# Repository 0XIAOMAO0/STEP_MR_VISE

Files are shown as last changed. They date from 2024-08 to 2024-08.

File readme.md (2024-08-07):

# 电动小台钳

## 项目介绍

本项目使用CNC板材及一些机械零件制作了一个电动焊接台钳。CNC器件在嘉立创1元CNC打样活动打样，驱动部分使用闭环步进驱动，电机驱动板适用35步进电机。可用于其他项目。计划实现功能

+ 台钳位置闭环

+ 按键设定位置

+ 夹持电流自动调整(待做)

+ 长时间自动休眠(待做)

+ 外面控制输入(待做)

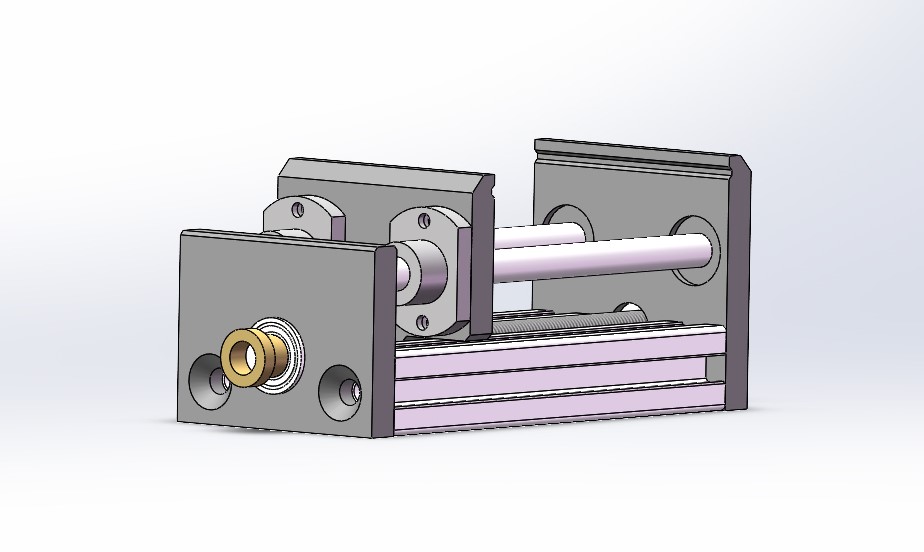
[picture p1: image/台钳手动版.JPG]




视频演示：[bilibili](https://www.bilibili.com/video/BV1ybicebESk/?share_source=copy_web&vd_source=d128331ee99153cf5294c26aba5f51e4) 

软件开源地址：[github](https://github.com/0XIAOMAO0/STEP_MR_VISE)   软件部分参考["矛盾聚合体"](https://gitee.com/STM32G474RET6/cl-stepper-motor)  

硬件开源地址: [oshwhub](http://oshwhub.com/xaiomao/tai-qian-kong-zhi-ban)硬件部分参考["HyperStepper"](https://oshwhub.com/HyperCNC/yi-ti-hua-di-cheng-ben-gao-su-gao-jing-du-quan-bi-huan-bu-jin-dian-ji)

## 材料清单

1.电路板所需元器件BOM已给出

2.结构部分：

|编号| 名称 | 个数 | 链接 |
|-|--- | ---- | --- |
| 1 |CNC铝板 | 3 | 嘉立创CNC打样 |
| 2 |2020铝型材120mm两端攻牙M6 | 2 | [参考连接]([欧标2020工业铝型材2040/2060/2080V槽黑色铝合金型材3D打印框架-淘宝网 (taobao.com)](https://item.taobao.com/item.htm?id=679620555797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..)) |
| 3 |8mm光轴130mm(两端不能有毛刺) | 2 | [参考链接]([45#钢直线导轨轴承20光轴镀铬棒加工高精度圆柱硬轴软轴活塞光杆-淘宝网 (taobao.com)](https://item.taobao.com/item.htm?id=707072898042&ft=t)) |
| 4 |双切边法兰直线轴承8x15x24 | 2 | [参考连接]([双切边椭圆法兰直线轴承中间型加长LMHC10 12 16 20 25 30 40 LUU-淘宝网 (taobao.com)](https://item.taobao.com/item.htm?id=674397062232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)) |
| 5 |T8丝杆143mm螺距2导程8 | 1 | [参考连接]([铭泰3d打印机配件T型T8丝杆步进电机丝杠螺母梯形螺杆不锈钢导程8-淘宝网 (taobao.com)](https://item.taobao.com/item.htm?id=573812002249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..)) |
| 6 |微型法兰轴承F688Z（8*18 *5） | 手动:2 / 电动:1 | [参考连接]([铭泰 3D打印机配件 微型带法兰直线轴承 F623 624 604 625 688ZZ-淘宝网 (taobao.com)](https://item.taobao.com/item.htm?id=574092180169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)) |
| 7 |消隙螺母T8导程8 | 1 | [参考连接]([3D打印机配件T8丝杆切边螺母铜消间隙消回差螺母梯型不锈钢丝杆-淘宝网 (taobao.com)](https://item.taobao.com/item.htm?id=648455763916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..)) |
| 8 |T8丝杆丝杆螺母螺距2导程8 | 1(一般买丝杆赠送) | [参考连接]([铭泰3d打印机配件T型T8丝杆步进电机丝杠螺母梯形螺杆不锈钢导程8-淘宝网 (taobao.com)](https://item.taobao.com/item.htm?id=573812002249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..)) |
| 9 |联轴器5*8 | 手动:0 / 电动:1 | [参考连接]([铭泰3D打印机配件铝合金联轴器 电机车膜船航模联轴器金属模型DIY-淘宝网 (taobao.com)](https://item.taobao.com/item.htm?id=570850575149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..)) |
| 10 |M6x14螺丝 | 4 |  |
| 11 |M3*12 *4(头径)小头螺丝 | 10 |  |
| 12 | 35步进电机 | 手动:0 / 电动:1 ||

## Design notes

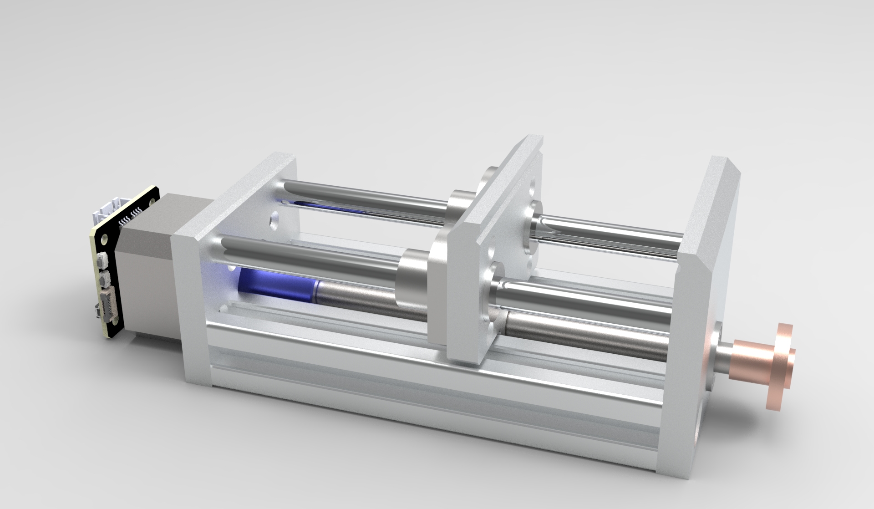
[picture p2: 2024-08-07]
image/渲染图.jpg

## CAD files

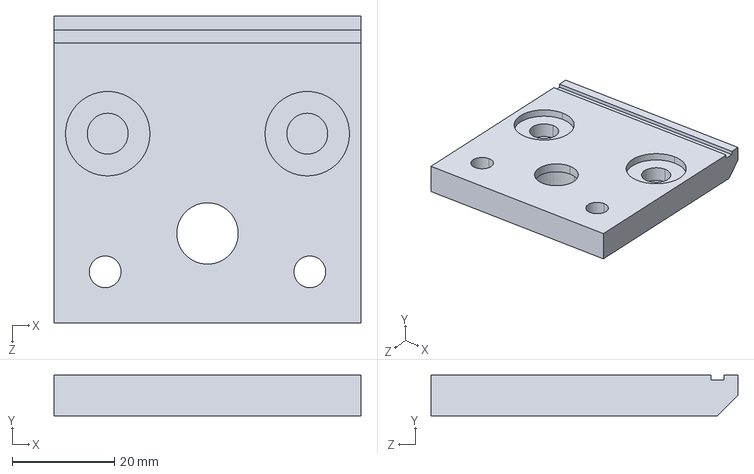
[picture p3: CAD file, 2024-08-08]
model/打样文件/修改版/修改版_固定钳身.STEP
60.0 x 8.00 x 60.0 mm

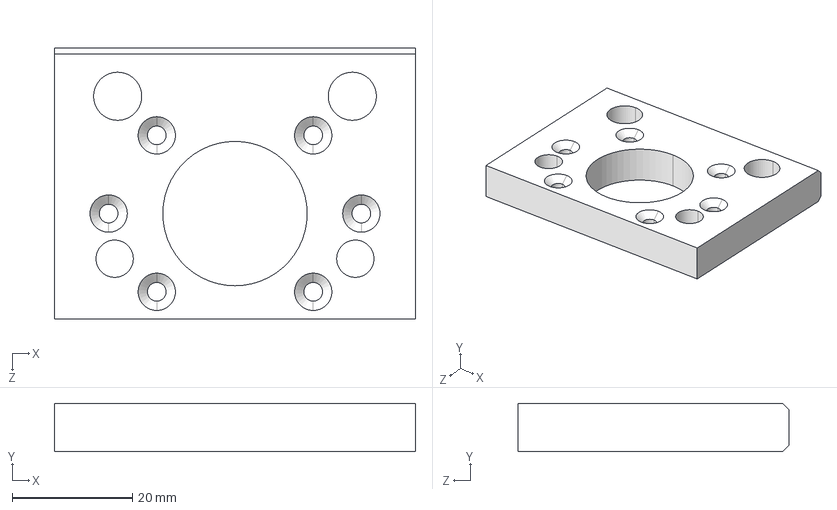
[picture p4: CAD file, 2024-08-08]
model/打样文件/原版/侧板.STEP
60.0 x 8.00 x 45.0 mm

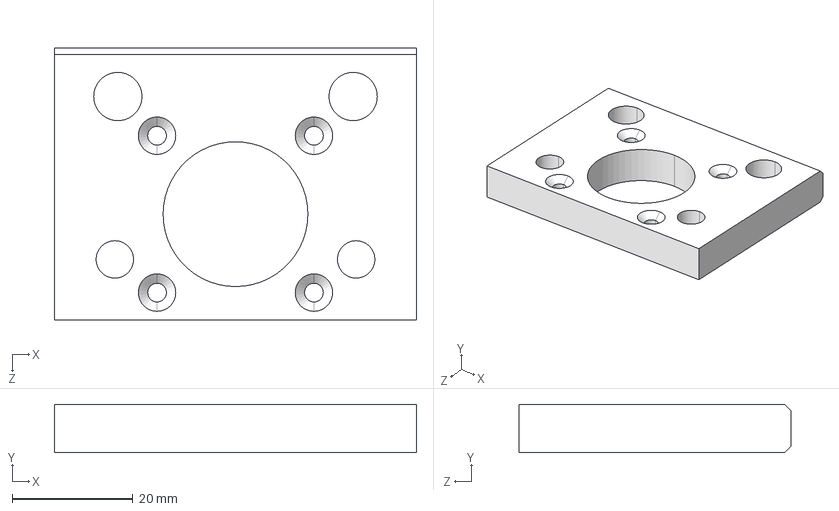
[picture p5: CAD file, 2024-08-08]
model/打样文件/修改版/修改版_侧板.STEP
60.0 x 8.00 x 45.0 mm

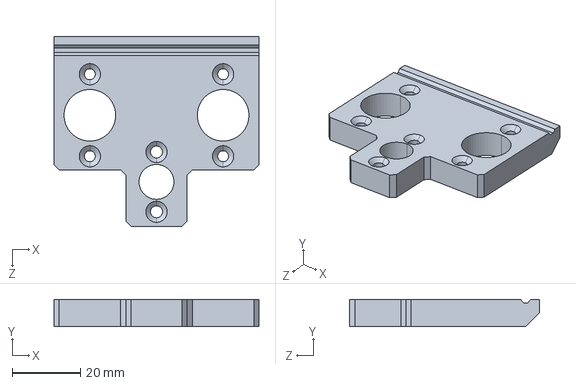
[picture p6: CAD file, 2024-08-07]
model/打样文件/原版/活动钳身.STEP
60.0 x 8.00 x 55.5 mm

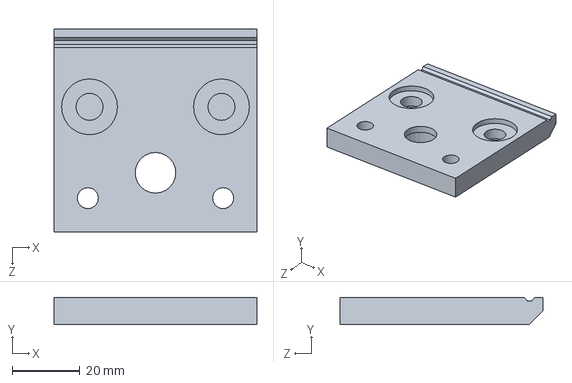
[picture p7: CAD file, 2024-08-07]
model/源文件/原版/固定钳身.SLDPRT
60.0 x 8.00 x 60.0 mm

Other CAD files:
model/源文件/修改版/修改版_固定钳身.SLDPRT
model/源文件/原版/侧板.SLDPRT
model/源文件/修改版/修改版_活动钳身.SLDPRT
model/打样文件/修改版/修改版_活动钳身.STEP
model/打样文件/原版/固定钳身.STEP
model/源文件/修改版/修改版_侧板.SLDPRT
model/源文件/原版/侧板_手动板.SLDPRT
model/打样文件/修改版/侧板_手动板.STEP
model/打样文件/原版/侧板_手动板.STEP
model/源文件/修改版/侧板_手动板.SLDPRT
model/源文件/原版/活动钳身.SLDPRT

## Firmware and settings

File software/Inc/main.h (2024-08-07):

#ifndef __MAIN_H__
#define __MAIN_H__

#include "stm32f0xx_ll_iwdg.h"
#include "stm32f0xx_ll_crs.h"
#include "stm32f0xx_ll_rcc.h"
#include "stm32f0xx_ll_bus.h"
#include "stm32f0xx_ll_system.h"
#include "stm32f0xx_ll_exti.h"
#include "stm32f0xx_ll_cortex.h"
#include "stm32f0xx_ll_utils.h"
#include "stm32f0xx_ll_pwr.h"
#include "stm32f0xx_ll_dma.h"
#include "stm32f0xx_ll_spi.h"
#include "stm32f0xx_ll_tim.h"
#include "stm32f0xx_ll_usart.h"
#include "stm32f0xx_ll_gpio.h"
#include "math.h"
#include "stdio.h"
#include "stdint.h"
#include "string.h"
#include "key.h"

#define MISO_Pin LL_GPIO_PIN_6
#define MISO_GPIO_Port GPIOA
#define MOSI_Pin LL_GPIO_PIN_7
#define MOSI_GPIO_Port GPIOA
#define CAL_Pin LL_GPIO_PIN_0
#define CAL_GPIO_Port GPIOA
#define CLOSE_Pin LL_GPIO_PIN_1
#define CLOSE_GPIO_Port GPIOA
#define SET2_Pin LL_GPIO_PIN_2
#define SET2_GPIO_Port GPIOA
#define SET1_Pin LL_GPIO_PIN_3
#define SET1_GPIO_Port GPIOA
#define CLKIN_Pin LL_GPIO_PIN_0
#define CLKIN_GPIO_Port GPIOB
#define CLKIN_EXTI_IRQn EXTI0_1_IRQn
#define DIRIN_Pin LL_GPIO_PIN_1
#define DIRIN_GPIO_Port GPIOB
#define DIRIN_EXTI_IRQn EXTI0_1_IRQn
#define ENIN_Pin LL_GPIO_PIN_2
#define ENIN_GPIO_Port GPIOB
#define ENIN_EXTI_IRQn EXTI2_3_IRQn
#define LED_Pin LL_GPIO_PIN_11
#define LED_GPIO_Port GPIOB
#define PWM1_Pin LL_GPIO_PIN_4
#define PWM1_GPIO_Port GPIOB
#define PWM2_Pin LL_GPIO_PIN_5
#define PWM2_GPIO_Port GPIOB
#define IN1_Pin LL_GPIO_PIN_8
#define IN1_GPIO_Port GPIOB
#define IN2_Pin LL_GPIO_PIN_9
#define IN2_GPIO_Port GPIOB
#define IN3_Pin LL_GPIO_PIN_7
#define IN3_GPIO_Port GPIOB
#define IN4_Pin LL_GPIO_PIN_6
#define IN4_GPIO_Port GPIOB
#define NSS_Pin LL_GPIO_PIN_4
#define NSS_GPIO_Port GPIOA
#define KEY1_Pin LL_GPIO_PIN_3
#define KEY1_GPIO_Port GPIOB
#define KEY2_Pin LL_GPIO_PIN_15
#define KEY2_GPIO_Port GPIOA


#ifndef NVIC_PRIORITYGROUP_0
    #define NVIC_PRIORITYGROUP_0         ((uint32_t)0x00000007) /*!< 0 bit  for pre-emption priority,
    4 bits for subpriority */
    #define NVIC_PRIORITYGROUP_1         ((uint32_t)0x00000006) /*!< 1 bit  for pre-emption priority,
    3 bits for subpriority */
    #define NVIC_PRIORITYGROUP_2         ((uint32_t)0x00000005) /*!< 2 bits for pre-emption priority,
    2 bits for subpriority */
    #define NVIC_PRIORITYGROUP_3         ((uint32_t)0x00000004) /*!< 3 bits for pre-emption priority,
    1 bit  for subpriority */
    #define NVIC_PRIORITYGROUP_4         ((uint32_t)0x00000003) /*!< 4 bits for pre-emption priority,
    0 bit  for subpriority */
#endif

#define HIGH        1
#define LOW         0

#define CAL     LL_GPIO_IsInputPinSet(CAL_GPIO_Port,  CAL_Pin)
#define CLOSE   LL_GPIO_IsInputPinSet(CLOSE_GPIO_Port, CLOSE_Pin)
#define SET1    LL_GPIO_IsInputPinSet(SET1_GPIO_Port, SET1_Pin)
#define SET2    LL_GPIO_IsInputPinSet(SET2_GPIO_Port, SET2_Pin)
#define ENIN    LL_GPIO_IsInputPinSet(ENIN_GPIO_Port, ENIN_Pin)
#define DIRIN   LL_GPIO_IsInputPinSet(DIRIN_GPIO_Port,DIRIN_Pin) 

#define LED_H     LL_GPIO_SetOutputPin(LED_GPIO_Port, LED_Pin)
#define LED_L     LL_GPIO_ResetOutputPin(LED_GPIO_Port, LED_Pin)
#define LED_F     LL_GPIO_TogglePin(LED_GPIO_Port, LED_Pin)
#define IN1_HIGH  LL_GPIO_SetOutputPin(IN1_GPIO_Port, IN1_Pin)
#define IN1_LOW   LL_GPIO_ResetOutputPin(IN1_GPIO_Port, IN1_Pin)
#define IN2_HIGH  LL_GPIO_SetOutputPin(IN2_GPIO_Port, IN2_Pin)
#define IN2_LOW   LL_GPIO_ResetOutputPin(IN2_GPIO_Port, IN2_Pin)
#define IN3_HIGH  LL_GPIO_SetOutputPin(IN3_GPIO_Port, IN3_Pin)
#define IN3_LOW   LL_GPIO_ResetOutputPin(IN3_GPIO_Port, IN3_Pin)
#define IN4_HIGH  LL_GPIO_SetOutputPin(IN4_GPIO_Port, IN4_Pin)
#define IN4_LOW   LL_GPIO_ResetOutputPin(IN4_GPIO_Port, IN4_Pin)

#define NSS_H   LL_GPIO_SetOutputPin(NSS_GPIO_Port, NSS_Pin)
#define NSS_L   LL_GPIO_ResetOutputPin(NSS_GPIO_Port, NSS_Pin)

#define SPI_TX_OD  LL_GPIO_SetPinOutputType(MOSI_GPIO_Port, MOSI_Pin, LL_GPIO_OUTPUT_OPENDRAIN)
#define SPI_TX_PP  LL_GPIO_SetPinOutputType(MOSI_GPIO_Port, MOSI_Pin, LL_GPIO_OUTPUT_PUSHPULL)


/* SPI command for TLE5012 */
#define READ_STATUS				0x8001			//8000
#define READ_ANGLE_VALUE		0x8021			//8020
#define READ_SPEED_VALUE		0x8031			//8030

#define WRITE_MOD1_VALUE		0x5060			//0_1010_0_000110_0001
#define MOD1_VALUE	0x0001

#define WRITE_MOD2_VALUE		0x5080			//0_1010_0_001000_0001
#define MOD2_VALUE	0x0800

#define WRITE_MOD3_VALUE		0x5091			//0_1010_0_001001_0001
#define MOD3_VALUE	0x0000

#define WRITE_MOD4_VALUE		0x50E0			//0_1010_0_001110_0001
#define MOD4_VALUE	0x0098						//9bit 512

#define WRITE_IFAB_VALUE		0x50B1
#define IFAB_VALUE 0x000D
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

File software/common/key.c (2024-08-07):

#include "key.h"
// #include "delay.h"

//////////////////////////////////////////////////////////////////////////////////

//// 按键初始化函数
//void KEY_Init(void)
//{
//	GPIO_InitTypeDef GPIO_Initure;

//	__HAL_RCC_GPIOA_CLK_ENABLE(); // 开启GPIOA时钟
//	__HAL_RCC_GPIOB_CLK_ENABLE(); // 开启GPIOC时钟

//	GPIO_Initure.Pin = GPIO_PIN_8;		  // PA8
//	GPIO_Initure.Mode = GPIO_MODE_INPUT;  // 输入
//	GPIO_Initure.Pull = GPIO_PULLUP;	  // 上拉
//	GPIO_Initure.Speed = GPIO_SPEED_HIGH; // 高速
//	HAL_GPIO_Init(GPIOA, &GPIO_Initure);

//	GPIO_Initure.Pin = GPIO_PIN_12 | GPIO_PIN_13 | GPIO_PIN_14 | GPIO_PIN_15; // PB12,13,14,15
//	GPIO_Initure.Mode = GPIO_MODE_INPUT;									  // 输入
//	GPIO_Initure.Pull = GPIO_PULLUP;										  // 上拉
//	GPIO_Initure.Speed = GPIO_SPEED_HIGH;									  // 高速
//	HAL_GPIO_Init(GPIOB, &GPIO_Initure);
//
#define PRESS_LONG_TIME  70 // 按键长按时间


uint8_t KEY_Scan(void)
{
	static uint8_t key_up = 1; // 按键按松开标志
	static uint8_t last_press = 0; // 上一次按下的按鍵
	static uint16_t press_time = 0; // 按键按下时间

	if (key_up && (KEY_1 == 0 || KEY_2 == 0 ))//首次按下
	{
		key_up = 0;
		if (KEY_1 == 0)
			last_press = KEY1_PRES;
		else if (KEY_2 == 0)
			last_press = KEY2_PRES;
		return 0;
	}

	if(key_up == 0)//上次有按鍵按下
	{	
		press_time ++;
		LL_mDelay(10);
		//printf("press_time:%d\r\n",press_time);
		if (KEY_1 == 1 && KEY_2 == 1) // 松开
		{
			key_up = 1;

			if(press_time > PRESS_LONG_TIME) //长按結束
			{
				press_time = 0;
				return 0;
			}
			press_time = 0;
			return last_press;
		}
		else if (KEY_1 == 0 && press_time > PRESS_LONG_TIME)//按下200ms以上，判定为长按
		{
			last_press = KEY1_PRES;
			return KEY1_LONG;
		}
		else if (KEY_2 == 0 && press_time > PRESS_LONG_TIME)
		{
			last_press = KEY2_PRES;
			return KEY2_LONG;
		}
	}
	return 0; // 无按键按下s
}


int8_t KEY_Process(void)
{
	uint16_t key_value = 0;
	key_value = KEY_Scan(); // 支持连按
	if (key_value == 0) return -1;
	// printf("key_value:%d\r\n",key_value);
	switch (key_value)
	{
	case KEY1_PRES:
		step_input += 6400/(stepangle/2.56f);//helf turn
		break;
	case KEY2_PRES:
		step_input -= 6400/(stepangle/2.56f);//helf turn
		break;
	case KEY1_LONG:
		step_input += 256/(stepangle/2.56f);
		break;
	case KEY2_LONG:
		step_input -= 256/(stepangle/2.56f);
		break;
	
	default:
		break;
	}
	return 0;
}

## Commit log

2024-08-04 [ADD] 按键控制模块添加
2024-08-07 添加模型文件
    [侧板.SLDPRT, 侧板.STEP, 侧板_手动板.SLDPRT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]
2024-08-08 修改模型符合活动规则
    [侧板.SLDPRT, 侧板.STEP, 侧板_手动板.SLDPRT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]
2024-10-13 添加编译好的固件
